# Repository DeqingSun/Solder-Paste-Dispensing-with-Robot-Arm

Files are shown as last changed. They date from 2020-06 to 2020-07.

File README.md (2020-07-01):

# Solder Paste Dispensing with Robot Arm

This is an open-sourced project that dispenses solder paste on PCB with a robot arm and Raspberry Pi. 

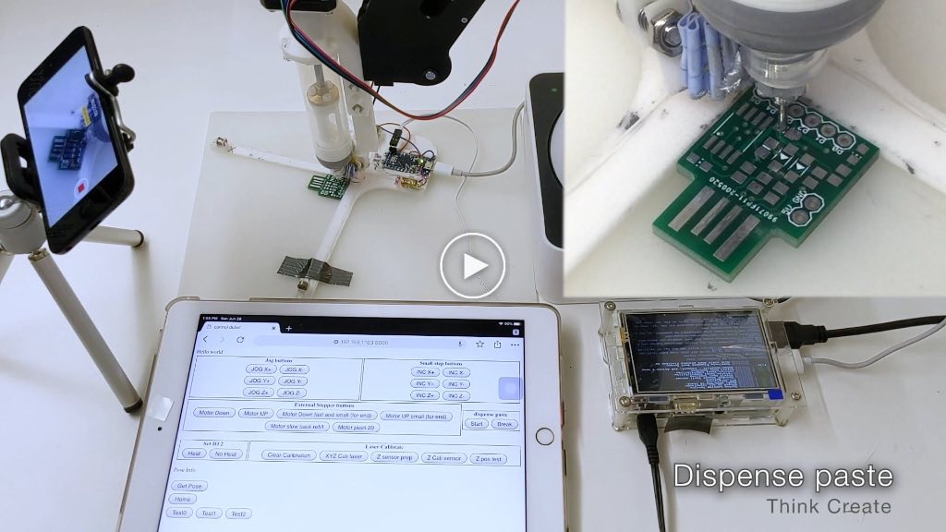
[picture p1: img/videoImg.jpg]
Demo Video (https://vimeo.com/433447125 "Demo Video")


This project uses an off-shelf Dobot Magician as the robot arm part. The customized end effector dispenses solder paste. And another laser jig calibrates the position of the robot arm. 

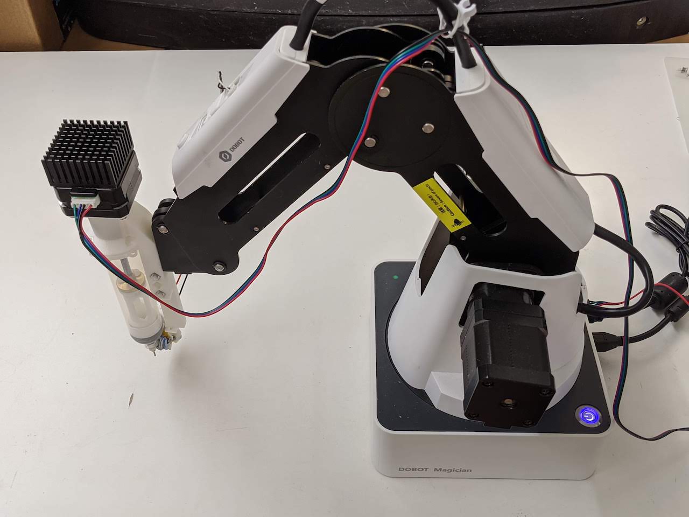
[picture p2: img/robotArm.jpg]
Dobot Magician with solder paste dispenser


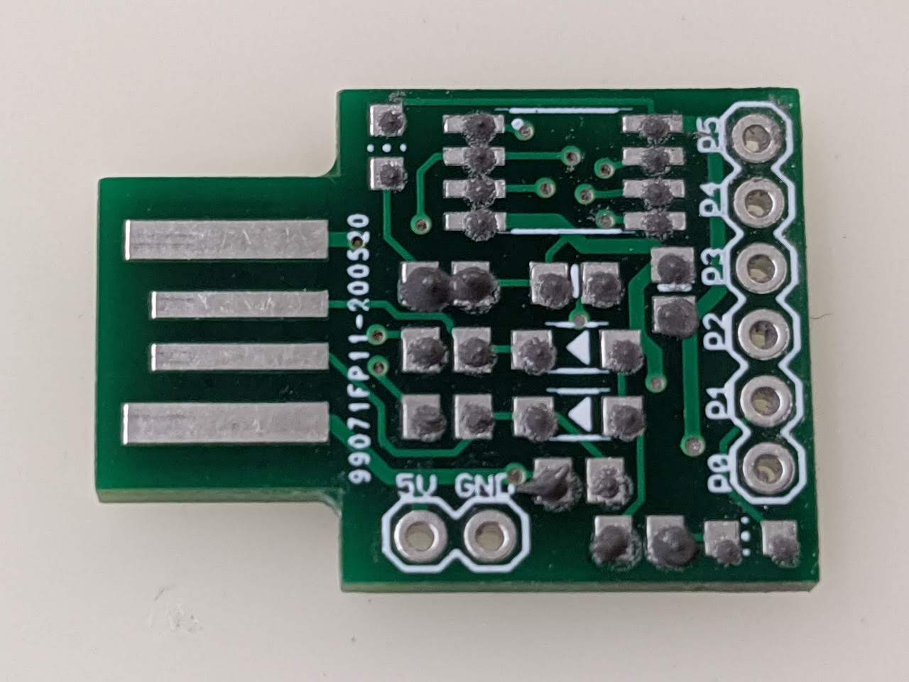
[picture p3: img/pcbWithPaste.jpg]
PCB with solder paste applied


## Hardware 

* Dobot Magician

A consumer-grade robot arm with an embed control box. 

* Raspberry Pi 3B

The Raspberry Pi is pretty convenient in playing with Python code. The Raspberry Pi hosted all files and run a python script. Users can use a browser on a computer or smartphone to control the robot arm with the Raspberry Pi. It's very easy to set up the Jupyter Notebook on the new version of Raspberry Pi OS, which saves a lot of time in debugging.

* 3D Printed Laser Jig

The laser jig uses 2 pairs of laser modules and photoresistors to calibrate the robot arm. There is also an auto-level sensor to fine-tune the Z-axis. The whole jig is controlled by an Arduino Micro Pro.

* 3D Printed solder paste dispenser

The solder paste dispenser is syringe driven by a stepper motor. There is also a heater attached to the needle to reduce the viscosity of the paste.

## Detail of the solder paste dispenser

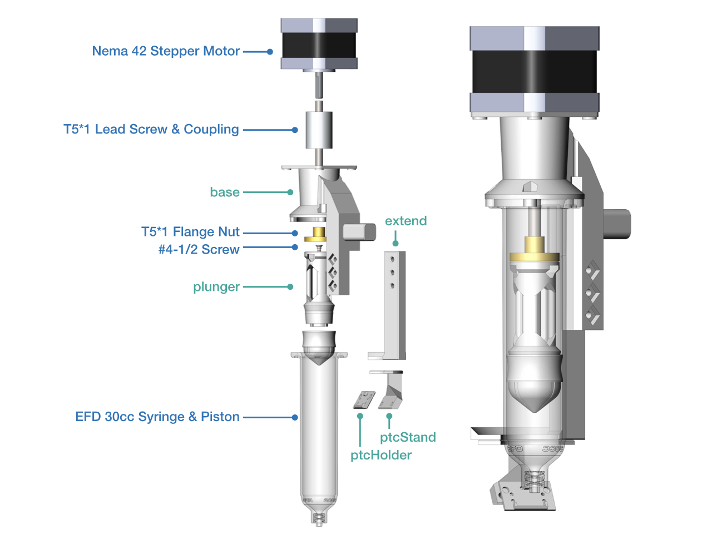
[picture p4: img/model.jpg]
img of dispenser


The solder paste dispenser uses a NEMA 42 stepper motor. Dobot Magician has 2 external motor drivers. However, the driving current is not adjustable. So a heatsink may be needed. The stepper is attached to a T5*1 leading screw with coupling, and the flange nut is attached to the piston with an adaptor and a #4-1/2 sheet metal screw. The syringe is a Nordson EFD 30cc one. And the needle is an 18 gauge one. Also, there is a 70C PTC heating element that keeps the needle warm to reduce the viscosity of the paste.

## Detail of the laser jig

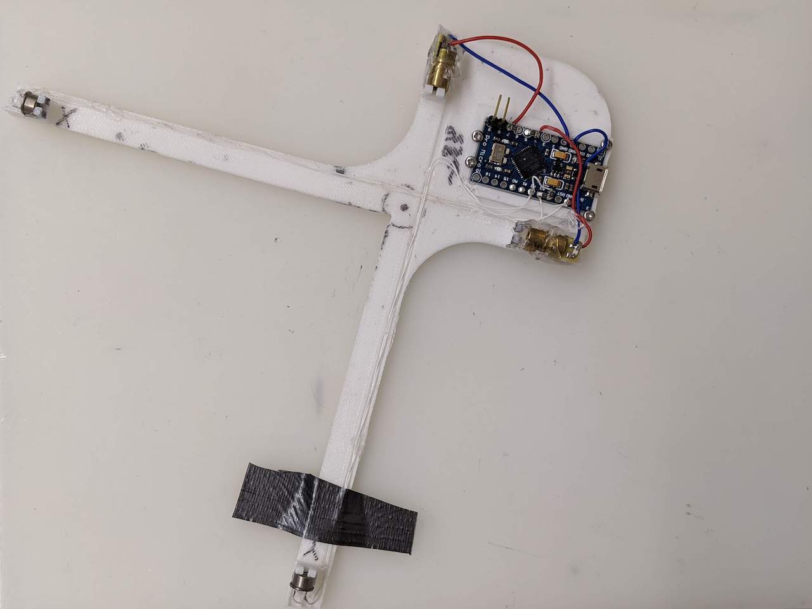
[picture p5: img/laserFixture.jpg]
laser jig


The laser jig is taped on a silicon pad for extra friction and Z-axis tolerance.  

## Why using a robot arm?

Most solder paste dispenser uses a Cartesian platform. A Cartesian platform is generally more accurate and rigid. But the machine is generally much bigger than its working area. The robot arm saves space. When the robot arm is not used, it only takes 40 sq in of desk space. Pretty neat for prototyping.    

## Why a laser jig?

A robot arm often has good repeatability and bad accuracy. With a laser-guided jig, the robot arm can get the position and orientation of target PCB accurately.

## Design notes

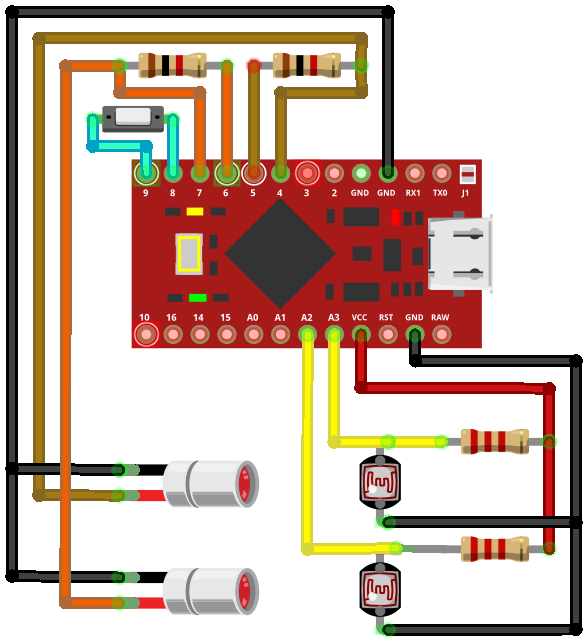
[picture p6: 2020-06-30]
laserJig/laserJigSch.png

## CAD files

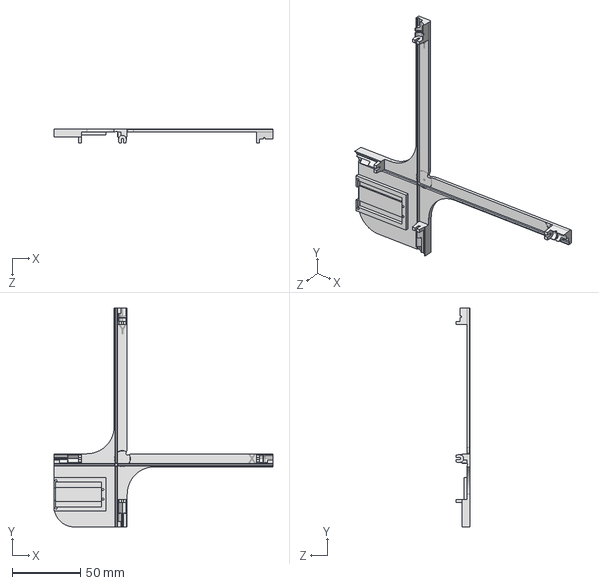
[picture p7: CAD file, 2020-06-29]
3D model/laserJig.STEP
160.0 x 160.0 x 10.5 mm

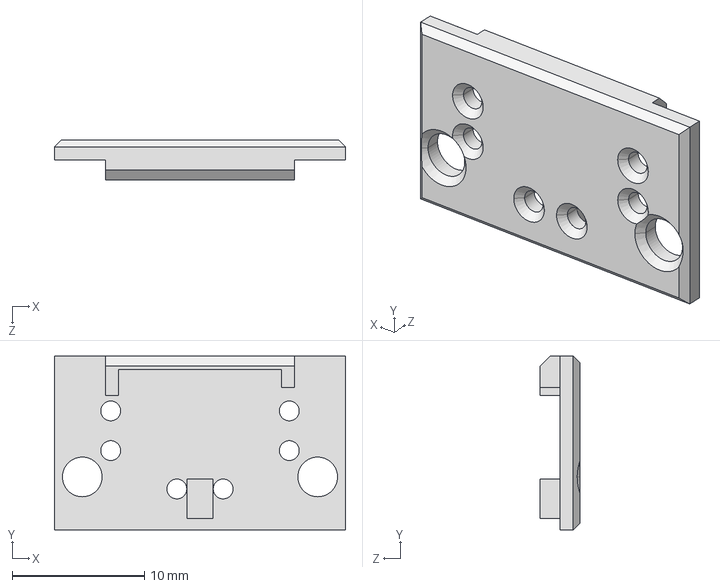
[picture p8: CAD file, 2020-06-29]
3D model/ptcHolder.STEP
22.0 x 13.2 x 3.00 mm

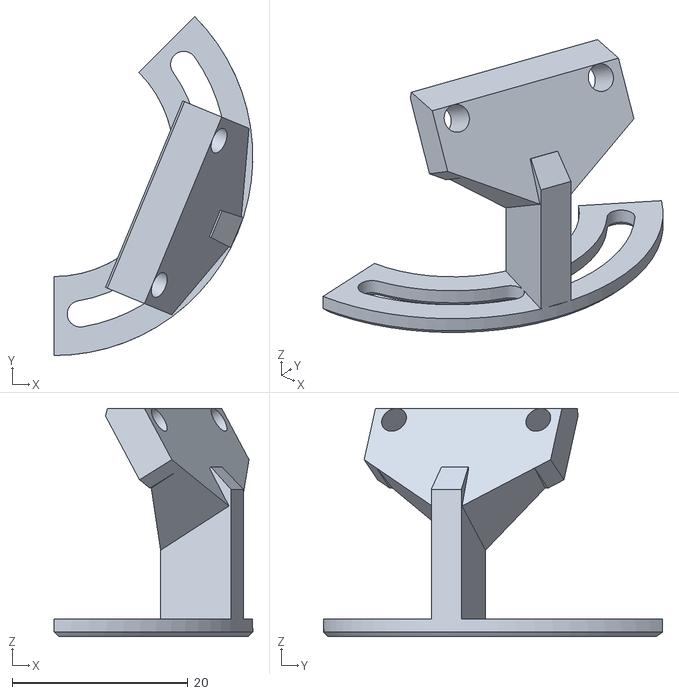
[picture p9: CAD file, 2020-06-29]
3D model/ptcStand.STL
22.6 x 38.6 x 26.0

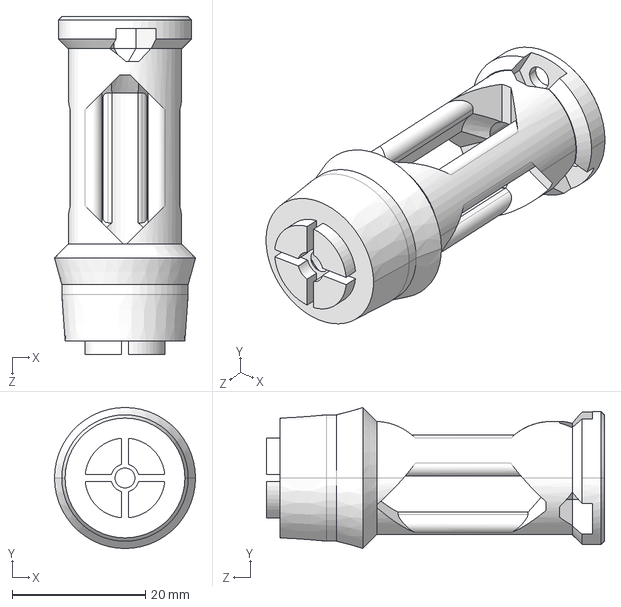
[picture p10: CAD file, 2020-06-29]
3D model/plunger.STEP
21.2 x 21.2 x 50.8 mm

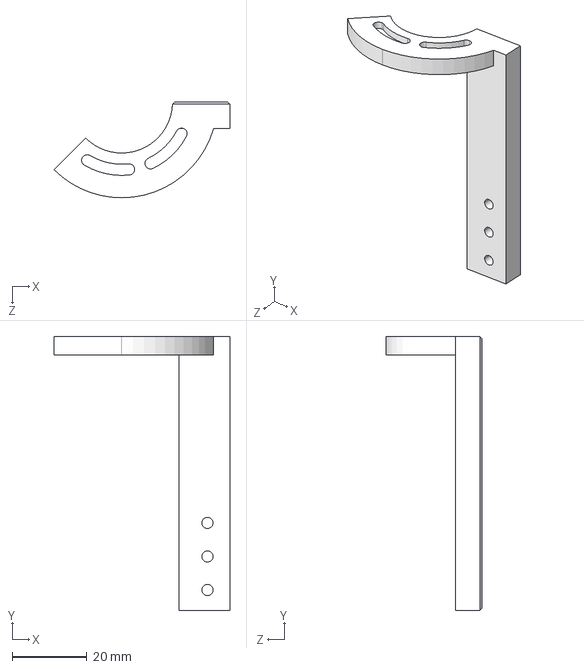
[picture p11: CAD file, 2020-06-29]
3D model/extend.STEP
47.1 x 73.5 x 25.6 mm

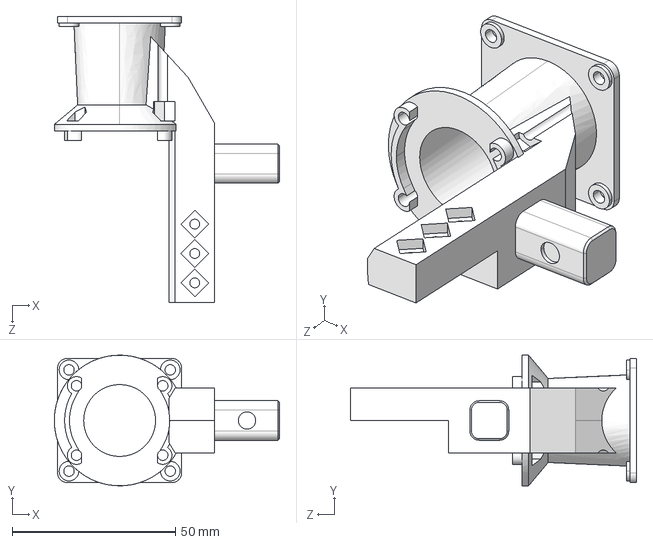
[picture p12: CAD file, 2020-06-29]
3D model/base.STEP
69.0 x 40.0 x 87.6 mm

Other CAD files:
3D model/ptcJoint.STEP
3D model/base.STL
3D model/extend.STL
3D model/laserJig.STL
3D model/plunger.STL
3D model/ptcHolder.STL

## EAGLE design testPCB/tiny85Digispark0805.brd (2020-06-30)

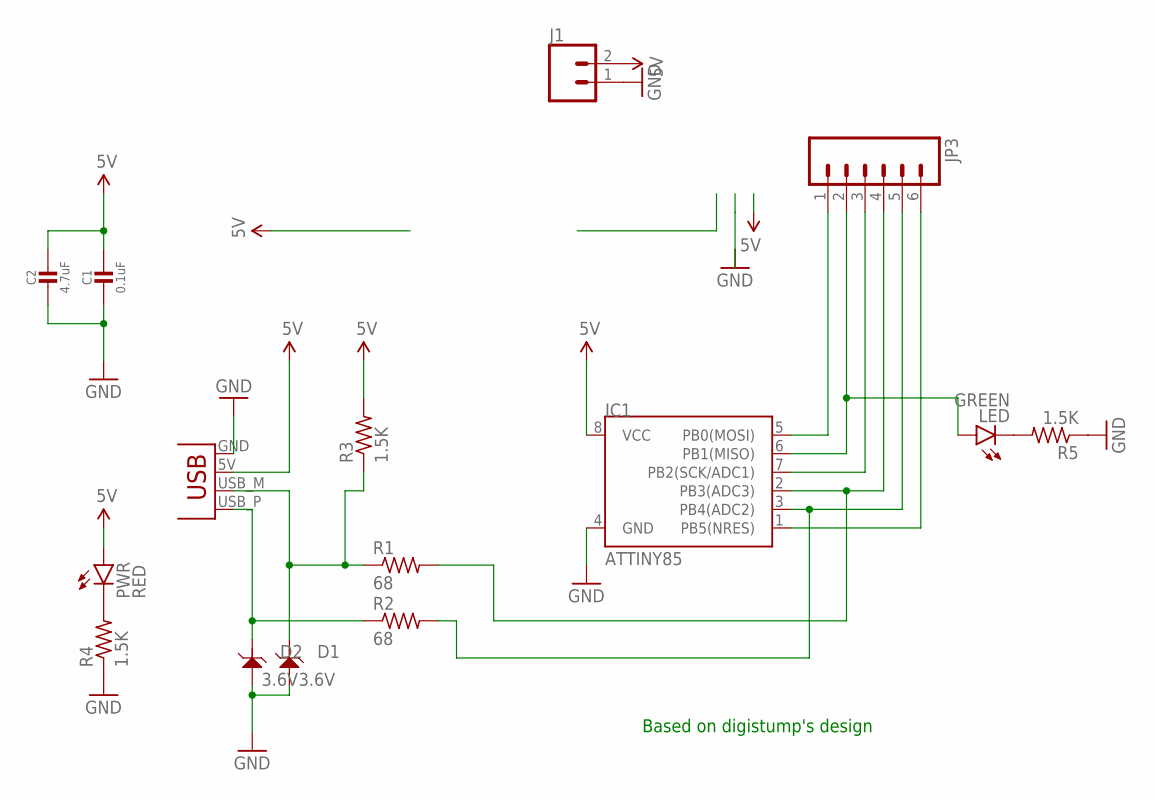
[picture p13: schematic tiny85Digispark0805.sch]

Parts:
C1: 0.1uF; 0805-NO
C2: 4.7uF; 0805-NO
D1, D2: 3.6V; SOD-123; LCSC C82565
IC1: ATTINY85; SO08-EIAJ
J1: CONN_02; 1X02
JP3: M06SIP; 1X06
LED: GREEN; CHIP-LED0805
PWR: RED; CHIP-LED0805
R1, R2: 68; M0805
R3, R4, R5: 1.5K; M0805
X1: USBPCB; USB-A-PCB

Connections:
5V: C1.1, C2.1, IC1.8 (VCC), J1.2, PWR.A, R3.2, X1.5V (VBUS)
GND: C1.2, C2.2, D1.+ (1), D2.+ (1), IC1.4 (GND), J1.1, R4.1, R5.1, X1.GND
unnamed: PWR.C, R4.2
unnamed: LED.C, R5.2
PB0: IC1.5 (PB0(MOSI)), JP3.1
PB1: IC1.6 (PB1(MISO)), JP3.2, LED.A
PB2: IC1.7 (PB2(SCK/ADC1)), JP3.3
PB3: IC1.2 (PB3(ADC3)), JP3.4, R1.2
PB4: IC1.3 (PB4(ADC2)), JP3.5, R2.2
PB5: IC1.1 (PB5(NRES)), JP3.6
USBM: D1.- (2), R1.1, R3.1, X1.USB_M (D-)
USBP: D2.- (2), R2.1, X1.USB_P (D+)

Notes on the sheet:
Based on digistump's design

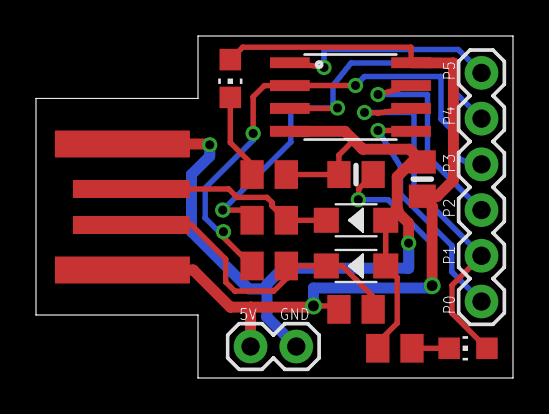
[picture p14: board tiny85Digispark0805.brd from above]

Board: 2 copper layers, 26.5 x 19.0 mm, 15 parts (0 on the bottom side), 12 nets.

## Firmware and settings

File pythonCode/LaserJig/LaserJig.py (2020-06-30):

import math,time, struct
from datetime import datetime
import serial

class LaserJig:
    def __init__(self,_dobot):
        self.dobot = _dobot
        
        available_ports = []
        for port in serial.tools.list_ports.comports():
            if (port.pid == 0x8036 and port.vid == 0x2341):
                available_ports.append(port.device)
        
        if len(available_ports)==0:
            print("No Arduino found")
            exit()
        self.ser = serial.Serial(None,
                         baudrate=115200,
                         parity=serial.PARITY_NONE,
                         stopbits=serial.STOPBITS_ONE,
                         bytesize=serial.EIGHTBITS,timeout = 0.01)
        self.ser.port = available_ports[0]
        
        self.calibrated = False
        self.sensorXIdle = None
        self.sensorYIdle = None
        self.jigZTouchpad = None
        
        #print("LaserJig init1")
        
        
    def dobotArcMovePrepare(self,x,y,z,r,radius,startAngle,travelAngle,wait = False):
        #self.dobot.move_to(x,y,z,r, wait=_wait)  #may not be needed in future
        endAngle = startAngle + travelAngle
        midAngle = startAngle + travelAngle*0.5
        startX = x+radius*math.cos(startAngle)
        startY = y+radius*math.sin(startAngle)
        self.midX = x+radius*math.cos(midAngle)
        self.midY = y+radius*math.sin(midAngle)        
        self.endX = x+radius*math.cos(endAngle)
        self.endY = y+radius*math.sin(endAngle)
        self.z = z
        self.r = r
        self.dobot.move_to(startX,startY,z,r, wait)

    def dobotArcMove(self,wait = False):
        response = self.dobot.arc_via_to(self.midX,self.midY,self.z,self.r,self.endX,self.endY,self.z,self.r, wait)
        expected_idx = struct.unpack_from('L', response.params, 0)[0]
        return expected_idx
    
    def dobotArcGetSensorData(self,x,y,z,r,radius,startAngle,travelAngle = math.pi*2*359/360):
        self.ser.open() #open port only when we need it. This helps solve the failure to read in second try.
        self.dobotArcMovePrepare(x,y,z,r,radius,startAngle,travelAngle, wait = True)
        self.ser.reset_input_buffer()
        self.ser.write(b'L\n');
        expected_idx = self.dobotArcMove()
        current_idx = 0
        self.ser.read_all()
        recvBuffer = ""
        while True:
            try:
                current_idx = self.dobot._get_queued_cmd_current_index()
            except:
                pass    #at end of home command, there is a huge delay, which means dobot will not respond for 1~2 seconds 
            if current_idx == expected_idx:
                break
            bytesData = self.ser.read_all()
            recvBuffer = recvBuffer + bytesData.decode("ascii", errors="ignore")
        firstNewLineIndex = recvBuffer.index('\r\n')
        lastNewLineIndex = recvBuffer.rindex('\r\n')
        dataLines = recvBuffer[firstNewLineIndex+2:lastNewLineIndex].split('\r\n')
        dataX = []
        dataY = []
        for line in dataLines:
            valuesStr = line.split(',')
            if len(valuesStr)==2:
                dataX.append(int(valuesStr[0]))
                dataY.append(int(valuesStr[1]))
        self.ser.write(b'S\n');
        self.ser.close()
        return [dataX,dataY]
        
        
    def measureLinePositionInterval(self, x, y, z, r, lineAngle,radius,sensorIndex):
        #do 2 circles.
        sensorDatas = self.dobotArcGetSensorData(x,y,z,r,radius,startAngle = lineAngle + math.pi/2 )
        dataArr1 = sensorDatas[sensorIndex]
        peaks1 = self.findPeaks(dataArr1) 
        sensorDatas = self.dobotArcGetSensorData(x,y,z,r,radius,startAngle = lineAngle + math.pi/2 + math.pi )
        dataArr2 = sensorDatas[sensorIndex]
        peaks2 = self.findPeaks(dataArr2)
        
        if (len(peaks1)==2 and len(peaks2)==2):
            interval1=peaks1[1]-peaks1[0]
            interval2=peaks2[1]-peaks2[0]
            #print("measureLinePositionInterval",interval1,interval2)
            return [interval1,interval2]
        else:
            print("not all 2 while test the line.!!!!",peaks1,peaks2)
            if (len(peaks1)!=2):
                print("dataArr1",len(dataArr1),min(dataArr1),max(dataArr1))
            if (len(peaks2)!=2):
                print("dataArr2",len(dataArr2),min(dataArr2),max(dataArr2))
            return None
        
    def estimateLinePosition(self, x, y, z, r, lineAngle,radius,sensorIndex): #x,y is center of estimation(test circle)
        #use 2 circles to calculate line position
        result = self.measureLinePositionInterval(x, y, z, r, lineAngle,radius,sensorIndex)
        if (result == None):
            print("something wrong in measureLinePositionInterval, maybe not trigger 2 times each?")
            return None
        diff = result[1]-result[0];
        if (abs(diff)<3):
            pass
        else:
            halfRatioAngle = math.pi*result[0]/(result[0]+result[1])
            step = radius*math.cos(halfRatioAngle)
            xInc = step*math.cos(lineAngle + math.pi/2 + math.pi)
            yInc = step*math.sin(lineAngle + math.pi/2 + math.pi)
            x += xInc
            y += yInc
        return [x,y]
    
    def getToLineCenter(self, x, y, z, r, lineAngle,radius,skipRough = False): #x,y is center of estimation(test circle)
        if not skipRough:
            #do one rough and one fine (2*2 circle)
            self.dobot.set_arc_speed(50,50); #rough
            result1 = self.estimateLinePosition(x,y, z, r,lineAngle,radius,sensorIndex=0)
            if (result1 == None):
                print("something wrong in rough estimateLinePosition")
                return None
            self.dobot.set_ptp_common_params(velocity=100, acceleration=50)  #restore move speed
            #self.dobot.move_to(result1[0], result1[1], z, r, True)
            #time.sleep(0.5)
        else:
            result1 = [x,y]
        self.dobot.set_arc_speed(10,50); #fine
        result2 = self.estimateLinePosition(result1[0], result1[1], z, r,lineAngle,radius,sensorIndex=0)
        if (result2 == None):
            print("something wrong in fine estimateLinePosition")
            return None
        self.dobot.set_ptp_common_params(velocity=100, acceleration=50)  #restore move speed
        #self.dobot.move_to(result2[0], result2[1], z, r, True)
        return [result2[0], result2[1]]

    def getCrossCenterStartAngle(self, x, y, z, r , radius, startAngle):
        while True:
            sensorDatas = self.dobotArcGetSensorData(x,y,z,r,radius,startAngle-math.pi/8,math.pi/4 )
            if ( (max(sensorDatas[0])<(self.sensorXIdle+100)) and (max(sensorDatas[1])<(self.sensorYIdle+100)) ):
                #seems no beam is blocked around start angle
                break
            else:
                startAngle+=math.pi/8
        return startAngle
    
    def getCrossCenterArc3Interval(self, x, y, z, r , radius, startAngle):
        startBeam = 0
        sensorDatas = self.dobotArcGetSensorData(x,y,z,r,radius,startAngle)
        peakX = self.findPeaks(sensorDatas[0])
        peakY = self.findPeaks(sensorDatas[1])
        if (len(peakX)!=2 or len(peakY)!=2):
            print("In getCrossCenterAndRoughRotation, not getting 2 blocks from each beam, try a better start point")
            #print(sensorDatas,peakX,peakY) #for debug
            return None
        if (peakX[0]<peakY[0] and peakY[0]<peakX[1] and peakX[1]<peakY[1]):
            #print("X triggered first, start angle within 2, 4 Quadrant or jig space")
            startBeam = 0
        elif (peakY[0]<peakX[0] and peakX[0]<peakY[1] and peakY[1]<peakX[1]):
            #print("Y triggered first, start angle within 1, 3 Quadrant or jig space")
            startBeam = 1
        else:
            print("In getCrossCenterAndRoughRotation, beams not triggered alternatively, try a better start point")
            print(peakX,peakY)
            return None        
        #print(peakX,peakY)
        allPeaks = sorted(peakX+peakY)
        interval = [allPeaks[1]-allPeaks[0],allPeaks[2]-allPeaks[1],allPeaks[3]-allPeaks[2]]
        return [startBeam, interval]
    
    def wrapRadianPMPi(self, angle):
        while (angle >= math.pi):
            angle -= math.pi*2;
        while (angle < -math.pi):
            angle += math.pi*2;
        return angle
    
    def meanAngle(self, angles):
        x = 0
        y = 0
        for angle in angles:
            x += math.cos(angle)
            y += math.sin(angle)
        return math.atan2(y, x)
    
    def closest(self, lst, K): 
        return lst[min(range(len(lst)), key = lambda i: abs(lst[i]-K))]
    
    def closestAngle(self, lst, K): 
        return lst[min(range(len(lst)), key = lambda i: abs(self.wrapRadianPMPi(lst[i]-K)))]
    
    def interpolatePoseDataWithNoneElements(self,inputData):
        elementWithValue = []
        for i in range(len(inputData)):
                if inputData[i]!=None:
                    elementWithValue.append(i)
        slopeBegin = (inputData[elementWithValue[1]]-inputData[elementWithValue[0]])/(elementWithValue[1]-elementWithValue[0])
        for i in range(elementWithValue[0]):
            inputData[i] = inputData[elementWithValue[0]]-slopeBegin*(elementWithValue[0]-i)
        #there is value in the end, no need to interpolate tail
        for j in range(len(elementWithValue)-1):
            slope = (inputData[elementWithValue[j+1]]-inputData[elementWithValue[j]])/(elementWithValue[j+1]-elementWithValue[j])
            for i in range(elementWithValue[j]+1,elementWithValue[j+1]):
                inputData[i] = inputData[elementWithValue[j]]-slope*(elementWithValue[j]-i)
        return inputData
    
    def getCrossCenterSlowSearch(self, x, y, z, r , radius, startAngle,travelAngle = math.pi*2*359/360, arcSpeed = 5):
        self.ser.open() #open port only when we need it. This helps solve the failure to read in second try.
        self.dobot.set_ptp_common_params(velocity=100, acceleration=50) 
        self.dobotArcMovePrepare(x,y,z,r,radius,startAngle,travelAngle, wait = True)
        self.ser.reset_input_buffer()
        self.ser.write(b'L\n');
        self.dobot.set_arc_speed(arcSpeed,100);
        expected_idx = self.dobotArcMove()
        current_idx = 0
        self.ser.read_all()
        recvBuffer = ""
        sensorDataX = []
        sensorDataY = []
        poseAngle = []
        
        cX, cY, cZ, cR, j1, j2, j3, j4=self.dobot.pose()
        pX = 0
        pY = 0
        while True:
            cX, cY, cZ, cR, j1, j2, j3, j4=self.dobot.pose()
            dist = abs(cX-pX)+abs(cY-pY)
            pX=cX
            pY=cY
            #print(cX, cY, dist)
            decodedData = self.ser.read_all().decode("ascii", errors="ignore")
            dataLines = (recvBuffer+decodedData).split('\r\n')
            recvBuffer = dataLines.pop()
            for line in dataLines:
                valuesStr = line.split(',')
                if len(valuesStr)==2:
                    try:
                        t1 = int(valuesStr[0])
                        t2 = int(valuesStr[1])
                        sensorDataX.append(t1)
                        sensorDataY.append(t2)
                        poseAngle.append(None)
                    except:
                        print("some non-critial error in parsing:"+line)
            poseAngle[-1] = math.atan2(cY-y,cX-x)
            
            if (dist)<0.1:
                break
        #print("DOBOT STOP MOVING")
        while True:
             try:
                 current_idx = self.dobot._get_queued_cmd_current_index()
             except:
                 pass    #at end of home command, there is a huge delay, which means dobot will not respond for 1~2 seconds 
             if current_idx == expected_idx:
                 break
        #print("Command completed")
        
        #1st data may be corrupted
        sensorDataX.pop(0)  
        sensorDataY.pop(0)
        poseAngle.pop(0)

        self.ser.write(b'S\n');
        self.ser.close()
        
        #interpolate poseAngle, because pose is slow
        
        roundVal = 0
        prevAngle = 0
        if (travelAngle>0):
            for i in range(len(poseAngle)):
                if poseAngle[i]!=None:
                    #print(poseAngle[i],poseAngle[i]+roundVal)
                    if ((poseAngle[i]+roundVal)<prevAngle):
                        roundVal += math.pi*2
                    poseAngle[i] += roundVal
                    prevAngle = poseAngle[i]
        else:
            for i in range(len(poseAngle)):
                if poseAngle[i]!=None:
                    #print(poseAngle[i],poseAngle[i]+roundVal)
                    if ((poseAngle[i]-roundVal)>prevAngle):
                        roundVal -= math.pi*2
                    poseAngle[i] -= roundVal
                    prevAngle = poseAngle[i]
                #print(poseAngle[i])
        
        #print(poseAngle)
        poseAngle = self.interpolatePoseDataWithNoneElements(poseAngle)
        peakXY = [self.findPeaks(sensorDataX),self.findPeaks(sensorDataY)]
        if (len(peakXY[0])!=2 or len(peakXY[1])!=2):
            print("In getCrossCenterSlowSearch, not getting 2 blocks from each beam, try a better start point")
            #print(sensorDatas,peakXY[0],peakXY[1]) #for debug
            return None
        if (peakXY[0][0]<peakXY[1][0] and peakXY[1][0]<peakXY[0][1] and peakXY[0][1]<peakXY[1][1]):
            #print("X triggered first, start angle within 2, 4 Quadrant or jig space")
            startBeam = 0
        elif (peakXY[1][0]<peakXY[0][0] and peakXY[0][0]<peakXY[1][1] and peakXY[1][1]<peakXY[0][1]):
            #print("Y triggered first, start angle within 1, 3 Quadrant or jig space")
            startBeam = 1
        else:
            print("In getCrossCenterSlowSearch, beams not triggered alternatively, try a better start point")
            print(peakXY[0],peakXY[1])
            return None        
        #print(peakXY[0],peakXY[1])
        peakXYLoc = [[],[]]
 
        for j in range(2):
            for i in peakXY[j]:
                angle = poseAngle[i]
                locX = x + radius*math.cos(angle)
                locY = y + radius*math.sin(angle)
                peakXYLoc[j].append( [locX,locY] )
                #self.dobot.move_to(locX, locY, z , r, True)
                #print(i,angle)
                #time.sleep(1)
        
        sumX = 0
        sumY = 0
        
        for j in range(2):
            for i in peakXYLoc[j]:
                sumX += i[0]
                sumY += i[1]
        
        centerX = sumX/4
        centerY = sumY/4
        
        #limit range
        xDir = [peakXYLoc[0][0][0]-peakXYLoc[0][1][0],peakXYLoc[0][0][1]-peakXYLoc[0][1][1]]
        yDir = [peakXYLoc[1][0][0]-peakXYLoc[1][1][0],peakXYLoc[1][0][1]-peakXYLoc[1][1][1]]
        #print(xDir,yDir)    
        angleX = math.atan2(xDir[1],xDir[0])
        angleY = math.atan2(yDir[1],yDir[0])
        
        if abs(self.wrapRadianPMPi(angleY-math.pi*0.5-angleX))<(math.pi/10):
            angle = self.meanAngle([angleY-math.pi*0.5,angleX])
        elif abs(self.wrapRadianPMPi(angleY+math.pi*0.5-angleX))<(math.pi/10):
            angle = self.meanAngle([angleY+math.pi*0.5,angleX])
        else:
            print("the calulated XY beam directions are not perpendicular:"+str(angleX)+","+str(angleY))
            return None
            
        if (angle>math.pi*.4 or angle<math.pi*-0.9):
            angle += math.pi #use outward direction
        elif (angle>math.pi*-0.5 and angle<math.pi*0.1):
            angle = angle
        else:
            print("Please put opening of jig outward")
            return None

        #using sensorData to calculate again, we are using ratio of intervals between peaks, to calculate x,y(center of test circle) in jig coordinates,
        #then we use angle to calulate jig zero in robot coordinates
        allPeaks = sorted(peakXY[0]+peakXY[1])
        #get movementSpeed
        speedTP1 = int(0.25*len(poseAngle))
        speedTP2 = int(0.75*len(poseAngle))
        arcSpeed = ((poseAngle[speedTP2]-poseAngle[speedTP1])/(speedTP2-speedTP1))
        fullCircleTime = int(round(math.pi * 2 / arcSpeed))
        interval = [allPeaks[1]-allPeaks[0],allPeaks[2]-allPeaks[1],allPeaks[3]-allPeaks[2]]
        interval.append(fullCircleTime-sum(interval))
        
        xPosDirectionIndex = poseAngle.index(self.closestAngle( poseAngle, angle))
        xPosDirectionPeakIndex = allPeaks.index(self.closest( allPeaks, xPosDirectionIndex))    #find which interval is 1st quadrant in jig 
        #print(xPosDirectionPeakIndex)
        
        #print(fullCircleTime)
        #print(allPeaks)
        #print(interval)
        for i in range(xPosDirectionPeakIndex):
            interval.append(interval.pop(0))
        #print(interval)

        yOffsetInJigCor = radius*math.cos(math.pi*(interval[3]+interval[2])/fullCircleTime)
        xOffsetInJigCor = radius*math.cos(math.pi*(interval[1]+interval[2])/fullCircleTime)
        offsetInJigCorLen = math.sqrt(yOffsetInJigCor*yOffsetInJigCor+xOffsetInJigCor*xOffsetInJigCor)
        offsetInJigCorAngle = math.atan2(yOffsetInJigCor,xOffsetInJigCor)
        
        offsetInRobotCorAngle = offsetInJigCorAngle + angle
        
        jigCenterX = x-offsetInJigCorLen*math.cos(offsetInRobotCorAngle)
        jigCenterY = y-offsetInJigCorLen*math.sin(offsetInRobotCorAngle)

        #print("x,y",x,y)
        #print("xOffsetInJigCor,yOffsetInJigCor",xOffsetInJigCor,yOffsetInJigCor)
        #print("offsetInJigCorLen,offsetInJigCorAngle",offsetInJigCorLen,offsetInJigCorAngle)
        #print("offsetInRobotCorAngle",offsetInRobotCorAngle)
        #print("use cor",centerX, centerY, angle)
        #print("jigCenter",jigCenterX,jigCenterY)
        #self.dobot.move_to(jigCenterX, jigCenterY, z , r, True)
        #time.sleep(5)

        #self.dobot.move_to(centerX, centerY, z , r, True)
        #time.sleep(5)
        #self.dobot.move_to(centerX+radius*2*math.cos(angle), centerY+radius*2*math.sin(angle), z , r, True)
        #time.sleep(5)
        #print(poseAngle)
        
        #return [centerX, centerY, angle]
        return [jigCenterX, jigCenterY, angle]
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

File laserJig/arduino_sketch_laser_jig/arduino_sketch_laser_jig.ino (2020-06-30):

String inputString = "";         // a string to hold incoming data
boolean stringComplete = false;  // whether the string is complete

unsigned long previousMillis = 0;
unsigned long laserStartMillis = 0;
unsigned long touchpadStartMillis = 0;
bool laserDetecting = false;
bool touchpadDetecting = false;

#define LASER_TIMEOUT  30000
#define TOUCHPAD_TIMEOUT  30000

#define LASER_ON {digitalWrite(5, HIGH);digitalWrite(6, HIGH);}
#define LASER_DIM {analogWrite(5, 5);analogWrite(6, 5);}

void setup() {
  // put your setup code here, to run once:
  LASER_DIM;
  Serial.begin(115200);
  pinMode(9, OUTPUT);
  digitalWrite(9, LOW);
  pinMode(8, INPUT);
  digitalWrite(8, HIGH);
}

void loop() {
  // put your main code here, to run repeatedly:
  unsigned long currentMillis = millis();

  if (laserDetecting) {
    if ((signed long)(currentMillis - previousMillis) >= 10) {
      previousMillis = currentMillis;
      Serial.print(analogRead(3));
      Serial.print(',');
      Serial.println(analogRead(2));
      if ((signed long)(currentMillis - laserStartMillis) >= LASER_TIMEOUT) {
        LASER_DIM;
        laserDetecting = false;
      }
    }
  }

  if (touchpadDetecting) {
    if ((signed long)(currentMillis - previousMillis) >= 10) {
      previousMillis = currentMillis;
      Serial.println(digitalRead(8));
      if ((signed long)(currentMillis - touchpadStartMillis) >= TOUCHPAD_TIMEOUT) {
        touchpadDetecting = false;
      }
    }
  }


  while (Serial.available()) {
    // get the new byte:
    char inChar = (char)Serial.read();
    // add it to the inputString:
    inputString += inChar;
    // if the incoming character is a newline, set a flag
    // so the main loop can do something about it:
    if (inChar == '\n') {
      stringComplete = true;
      break;
    }
  }

  if (stringComplete) {
    inputString.trim();
    char firstChar = inputString.charAt(0);
    if (firstChar == 'L') {
      LASER_ON;
      laserStartMillis = millis();
      touchpadDetecting = false;
      laserDetecting = true;
    } else if (firstChar == 'T') {
      touchpadStartMillis = millis();
      laserDetecting = false;
      touchpadDetecting = true;
    } else if (firstChar == 'S') {
      LASER_DIM;
      laserDetecting = false;
      touchpadDetecting = false;
    }
    inputString = "";
  }

}

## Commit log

2020-06-29 add 3d model
    [base.STEP, base.STL, extend.STEP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]
2020-06-30 add laser jig and code
    [laserJigSch.fzz]
2020-06-30 add python code and PCB files
    [tiny85Digispark0805.brd, tiny85Digispark0805.csv, tiny85Digispark0805.sch]

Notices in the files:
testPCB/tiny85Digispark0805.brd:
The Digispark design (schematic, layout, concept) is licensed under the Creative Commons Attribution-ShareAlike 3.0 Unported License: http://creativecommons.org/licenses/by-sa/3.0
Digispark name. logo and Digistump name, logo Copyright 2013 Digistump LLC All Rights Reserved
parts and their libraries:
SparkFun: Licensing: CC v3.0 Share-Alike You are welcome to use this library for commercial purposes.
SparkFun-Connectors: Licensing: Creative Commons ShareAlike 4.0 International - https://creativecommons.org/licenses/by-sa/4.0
